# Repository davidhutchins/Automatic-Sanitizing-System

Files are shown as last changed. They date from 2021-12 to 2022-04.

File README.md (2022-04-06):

# Automatic-Sanitizing-System
## IoT Automatic Door-Handle Cleaning System

By David Hutchins, Austin Welch, Branden Evangelista, Alejandro Jacobo, and Brontë Cadogan

## Synopsis
The Automatic Handle Cleaning System (A.H.C.S. for short) is a senior design project that attempts to help make the world a more sanitary place. Inspired by the COVID-19 pandemic and its call for a higher degree of sanitation, the A.H.C.S. uses embedded electronics and UV-C lights to detect motion and disinfect door handles as people use them. The entire system is battery powered, allowing for its use to disinfect any door handle, anywhere. The A.H.C.S. is internet enabled, and each device sends its sensor data to the A.H.C.S. server, which allows user accounts to monitor each of their devices and track usage data. Users can use this data to better understand traffic throughout each of their buildings and learn how frequently each door is used over time. 

## Setup Guide
This guide is intended to help you set up your Automatic Handle Cleaning System (AHCS) device, connect it to the internet, and link it with your AHCS account. 

### Step 1: Power on AHCS in configuration mode
In this step, you will turn on the AHCS in configuration mode, where you can then edit its configuration settings. 
1.	Power off the AHCS if it is already on.
2.	Find the configuration button located on the top right of the AHCS and hold it down.
3.	While holding down the configuration button, power on the AHCS.
4.	If successful, the front-facing LED should now be lit yellow.
 
### Step 2: Enter the configuration webpage
This step will show you how to connect to your AHCS device and how to access its configuration page. 
1.	Once the LED is lit yellow, the AHCS will be hosting an Access Point (AP) through which you can connect to with any Wi-Fi enabled device with access to an internet browser (i.e. Chrome, Firefox, Safari).
2.	Connect to the AP named “AHCS-ID” where ID will be replaced with your device’s ID number. 
3.	Once connected, your device might say that your connection does not have internet access, this is okay. 
4.	In a browser, enter the URL handlesetup.net and proceed to the webpage. 
5.	Once the page loads, you can continue to the next step. 

### Step 3: Edit your AHCS’s configuration settings
In the configuration webpage, you can change the AHCS’s Wi-Fi configuration and take note of its ID and registration code. 
1.	Configure your AHCS’s Wi-Fi configuration under the Wi-Fi Configuration tab.
2.	Current SSID and Security correspond to the current network the AHCS is connected to and that network’s security settings.
3.	Enter the SSID, security type, and password of the network you want to connect to and click ‘Apply’. The Current SSID and Security variables at the top will then change.
4.	Head to the Registration tab and take note of the Registration Code and Device ID as these will be needed for the next step.
5.	Click ‘Exit and Restart Device’, the AHCS will then restart and attempt to connect to the Wi-Fi network it was configured to. This will take 15-30 seconds. 
6.	Upon successful connection, the AHCS’s front LED will turn blue. If it cannot connect to the network, it will turn green. If the light turns green start again from step 1 and try again, making sure all the configuration settings were set correctly. 
7.	If the LED is blue, continue to the next step. 

### Step 4: Link AHCS with account
Once the AHCS has connected to a network for the first time, you will be able to link the device to your account.
1.	Go to the AHCS website at http://3.91.185.66/ and sign in to your account. If you do not have one, make sure to create a new account before continuing. 
2.	Once signed in, navigate to the Add Device section on the homepage. 
3.	Enter the AHCS Device ID and Registration/Verification Code from earlier and select ‘Add Device’. 
4.	If successful, you will receive a prompt saying that the link was successful, if not, ensure you have connected your AHCS device to the internet at least once and you correctly entered the AHCS ID and Registration/Verification code. 
5.	Congratulations! You have successfully connected your AHCS device to the internet and linked it to your account! You can now view the AHCS device’s statistics and data on the ‘Sanitizing Statistics’ page. 

## For Development and Testing
### Embedded Code
#### Install CCS
1. Download CCS from https://www.ti.com/tool/download/CCSTUDIO
2. Proceed through the installer, when asked to select between full and custom installation, choose custom and click next
3. On 'Select Components' Select 'SimpleLink MSP432 low power + performance MCUs'
4. On the next page, select only 'Spectrum Digital Debug Probes and Boards'
5. Proceed until program is installed

#### In CCS
1. Go to File > Import 
2. Choose Code Composer Studio > CCS Projects
3. Clone/Download the repository and select Hardware > Hand-Sanitizing-System as the search directory
4. Select Hand-Sanitizing-System_MSP432 and Finish
5. Hit the hammer icon on the top left bar to build the project (if it is not compiling, ensure that (Active - Debug) appears next to the project name on the project explorer, you can do this by clicking on the project, which 'selects' it as the build target)

### Running the Automatic Hand Cleaning System App (Webapp) on a Local Machine
1. Make sure NodeJS is installed https://nodejs.org/en/
2. Download the repo from GitHub using 
    `git clone https://github.com/davidhutchins/Automatic-Sanitizing-System.git`
3. Install dependencies using: `npm i`
4. Open the command prompt and navigate to the folder containing the server.js file:
   `cd Automatic-Sanitizing-System/Server/sanitizingsystem/src/server`
5. Enter the command `node server.js` to connect to the MongoDB database
6. In another terminal, navigate to this folder:
   `cd Automatic-Sanitizing-System/Server/sanitizingsystem/src`
and run the application with `npm start`
7. In another terminal, navigate to this folder:
   `cd Automatic-Sanitizing-System/Server/sanitizingsystem/src`
and enter the command `node exserver.js` to connect to the Express backend

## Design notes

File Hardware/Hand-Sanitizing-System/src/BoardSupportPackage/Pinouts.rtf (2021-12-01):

HFXT
In: PJ.3
Out: PJ.2

LED I2C
SDA: P3.6
SCL: P3.7

SensorPack I2C
SDA: P6.4
SCL: P6.5

SensorPack OPT3001
IRQ Pin: P3.6

SensorPack TMP007
IRQ Pin: P5.2

SensorPack BMI160
IRQ Pin: P4.1 // Disabled for CC3100
MAG IRQ Pin: P4.6

SensorPack BME280
IRQ Pin: P5.0

LaunchPad
Reset Pin: RST
RED LED: P1.0
Red RGB LED: P2.0
Green RGB LED: P2.1
Blue RGB LED: P2.2
Left Button: P1.1
Right Button: P1.4

Joystick
X-axis: P6.0
Y-axis: P6.1
Press: P4.3

Buttons
Up: P4.4
Right: P4.5
Down: P5.4
Left: P5.5

CC3100
IRQ: P2.5
ANT1: P2.7
ANT2: P2.6
CS: P3.0
HIB: P4.1
CLK: P1.5
MOSI: P1.6
MISO: P1.7

LCD
TFT_CS P10.4
TP_CS P10.5
CLK P10.1
DIN P10.3
DOUT P10.2
TP_IRQ P4.0
Reset P10.0
Backlight VCC

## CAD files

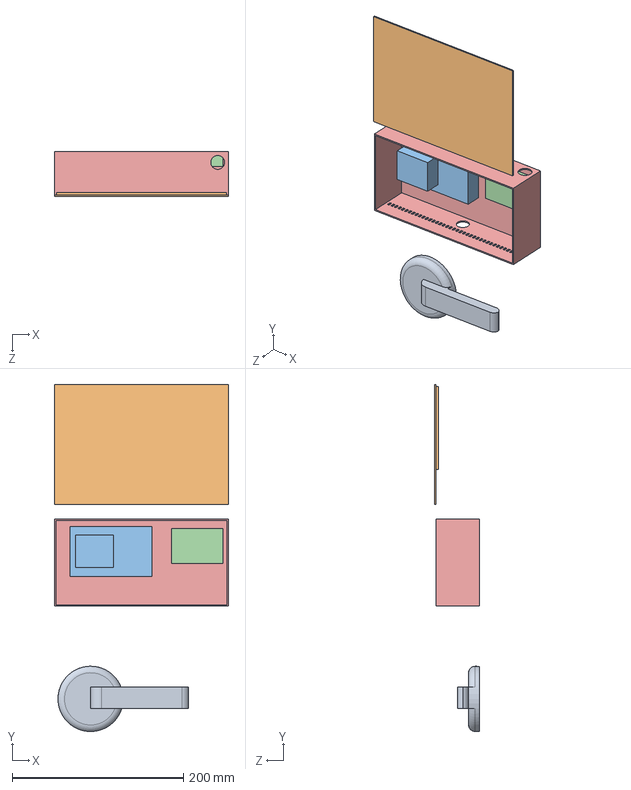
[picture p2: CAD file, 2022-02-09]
3-D Schematics/Assembly/Mockup_Assembly.SLDASM
203.2 x 404.7 x 52.4 mm
DoorHandle
Lid_V3
MCU
Prototype_Board
Housing_V3

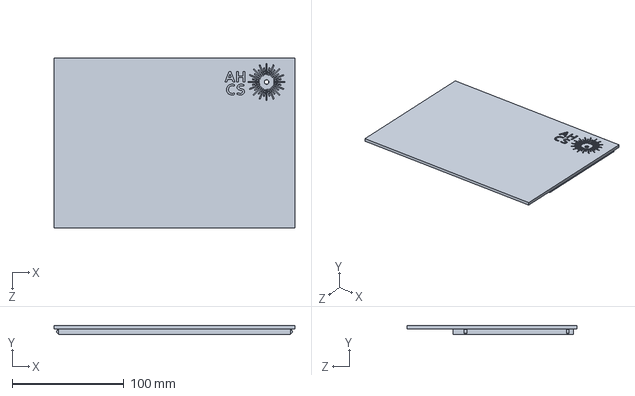
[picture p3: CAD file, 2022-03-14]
3-D Schematics/Parts/Lid_V4.SLDPRT
215.9 x 8.13 x 152.4 mm

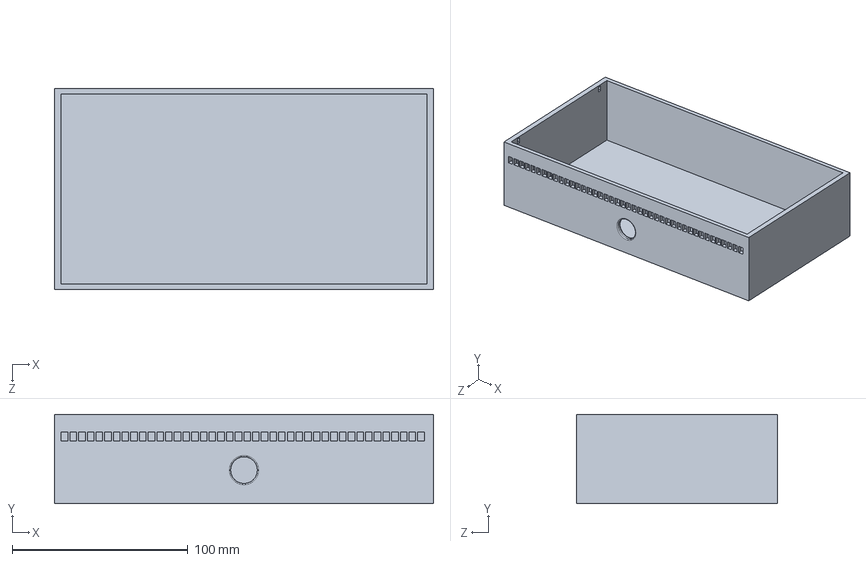
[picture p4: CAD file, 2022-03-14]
3-D Schematics/Parts/Housing_V4.SLDPRT
215.9 x 50.8 x 114.3 mm

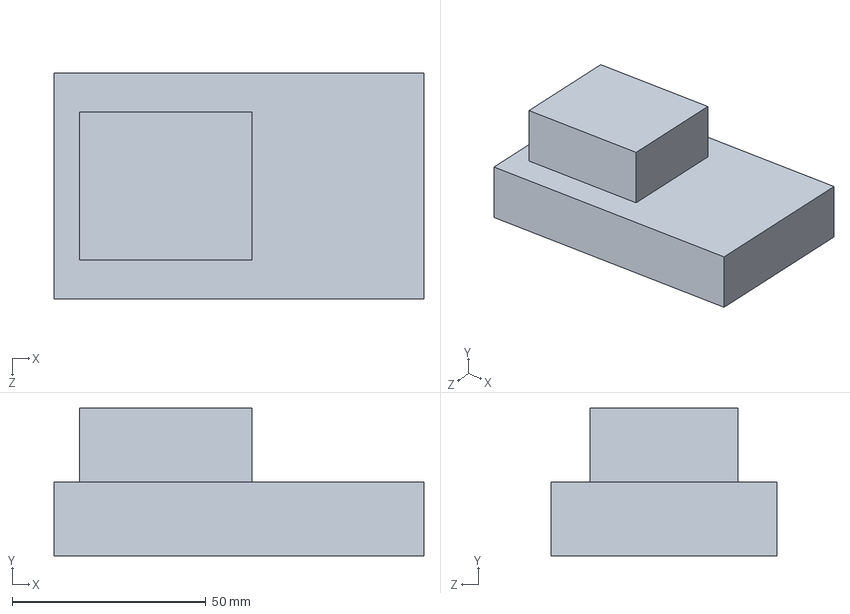
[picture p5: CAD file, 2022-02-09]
3-D Schematics/Parts/MCU.SLDPRT
95.5 x 38.1 x 58.4 mm

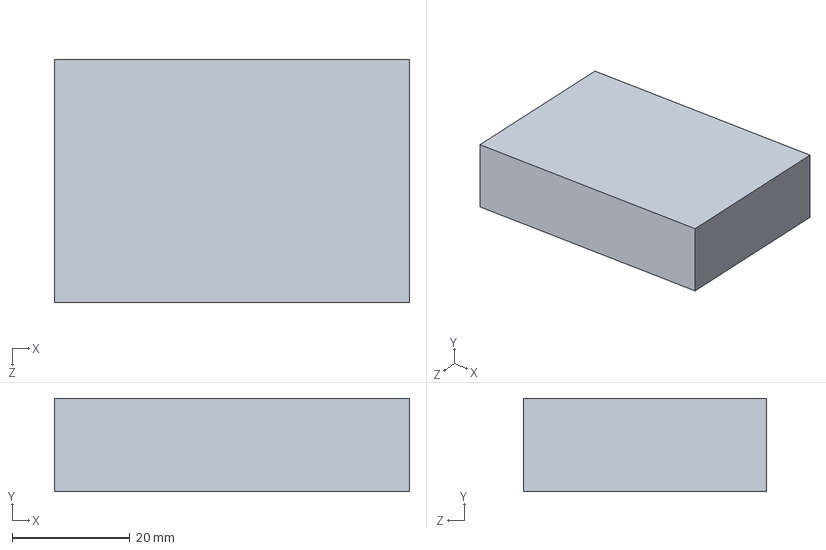
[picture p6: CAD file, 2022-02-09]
3-D Schematics/Parts/Prototype_Board.SLDPRT
60.3 x 15.9 x 41.3 mm

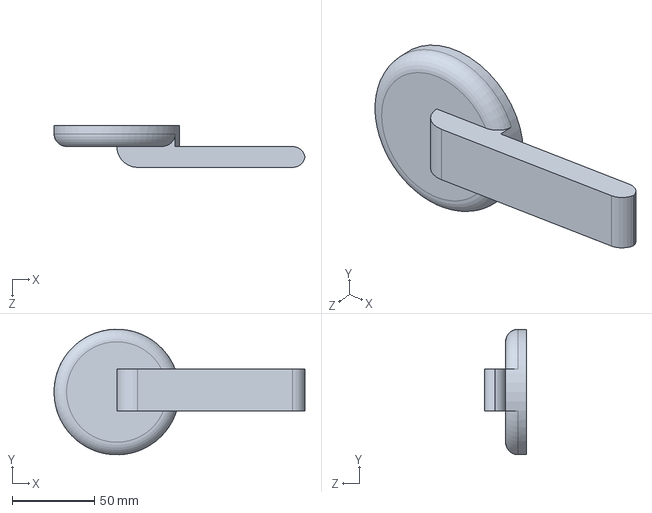
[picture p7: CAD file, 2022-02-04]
3-D Schematics/Parts/DoorHandle.SLDPRT
152.3 x 76.1 x 25.4 mm

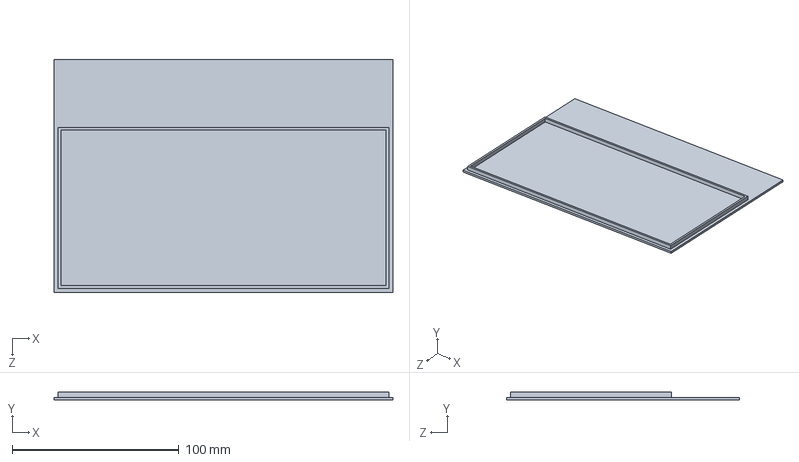
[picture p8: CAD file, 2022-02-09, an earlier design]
3-D Schematics/Parts/Lid_V3.SLDPRT
203.2 x 4.76 x 139.7 mm

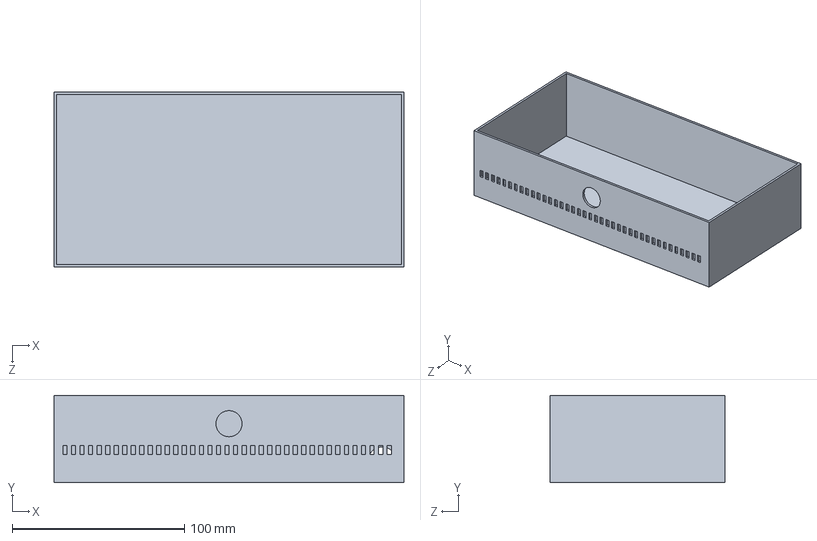
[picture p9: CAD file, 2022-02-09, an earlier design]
3-D Schematics/Parts/Housing_V3.SLDPRT
203.2 x 50.8 x 101.6 mm

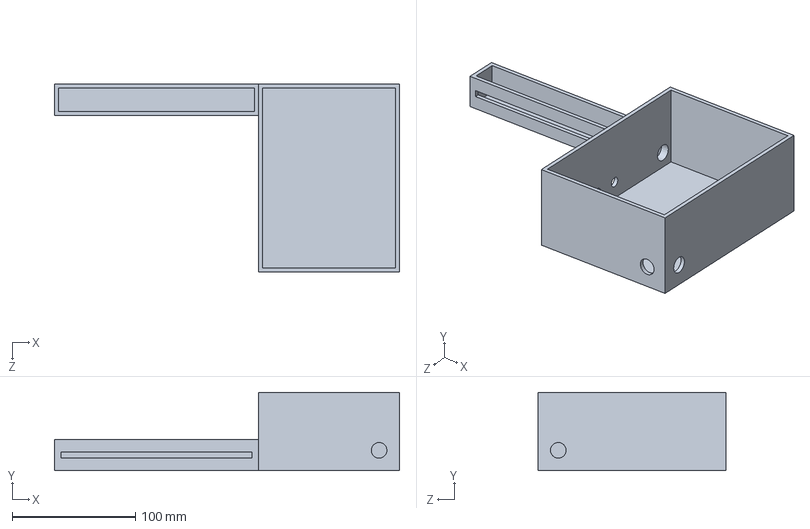
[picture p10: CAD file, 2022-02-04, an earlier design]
3-D Schematics/Parts/Housing_V1.SLDPRT
279.4 x 63.5 x 152.4 mm

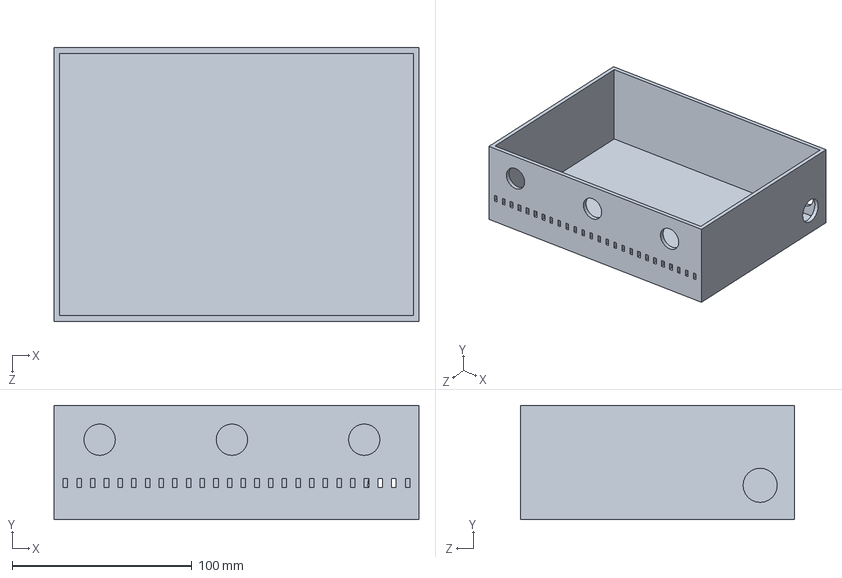
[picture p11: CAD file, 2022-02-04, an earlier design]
3-D Schematics/Parts/Housing_V2.SLDPRT
203.2 x 63.5 x 152.4 mm

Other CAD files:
3-D Schematics/Drawings/Housing_V4.SLDDRW
3-D Schematics/Drawings/Lid_V4.SLDDRW

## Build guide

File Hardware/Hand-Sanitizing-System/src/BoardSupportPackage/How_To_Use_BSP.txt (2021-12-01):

BSP Notes:

	Raz's Drivers

	BSP:
		Init Entire Board:
			BSP_InitBoard(): calls all subsequent initialization functions

	ClockSys:
		Init: ClockSys_SetMaxFreq() (Sets MCLK to 48MHz, HSMCLK to 24MHz, and SMCLK to 12 MHz)
		Read Data: ClockSys_GetSysFreq() (Gets MCLK Speed in MHz) 

		Problems/Concerns: None at the momemnt
		Future Improvements: Configurability? (Difficult when trying to sync using peripherals)

	BackChannelUART
		Init: BackChannelInit(): Set's up backchannel UART to communicate at 115200 Baud with 1 Start bit, 8 data bis, and 1 Stop bit
		
		Print Text: BackChannelPrint(string, textStyle)
			Prints a string in json format with specfic textStyle enumeration

		BackChannelPrintIntVariable:
			Prints an integer variable name and value in json format

		BackChannelEventTrigger:
			Prints an event trigger in JSON format

	TI's Drivers

	Opt3001: (Light Sensor) 
		Init: [initI2C must be called beforehand] sensorOpt3001Enable(true)
		Read Data: sensorOpt3001Read(uint16_t *rawData)

		Problems/Concerns: Does not use interrupt to signal processor that data is ready. Simply returns false if failed. Wasted CPU time
		Future Improvements: Enable Port to receive intrrupts from sensor. Big CPU saver

	Tmp007:
		Init: [initI2C must be called beforehand] sensorTmp007Enable(true)
		Read Data: sensorTmp007Read(uint16_t *rawTemp, uint16_t *rawObjTemp)

		Problems/Concerns: Does not use interrupt to signal processor that data is ready. Simply returns false if failed. Wasted CPU time
		Future Improvements: Enable Port to receive intrrupts from sensor. Big CPU saver

	Bosch's Drivers

	Bmi160:
		A LOT of things going on here. BoschSensorTec has some SUPER configurable code (resulting in tens of thousands of lines of code though -_-)

		There are 2 libraries: bmi160 and bmi160_support
			bmi160 is the full api containing every single possible function for messing with this thing. 
			bmi160_support contains example functions, public data structures, and compound api calls.

		Main Struct: bmi160_t - Holds valuable information such as chip id, device address, WriteFunctionPTR, ReadFunctionPTR, BurstWriteFunctionPtr, DelayMSFunction

		To Initialize the bmi160, you must first initialize the bmi160_t struct with all fields except chip id.
		Then Call bmi160_init which will test out the reading and writing as well as get the chip id and link the struct pointer into the library.

		*** ALL OF THIS CAN BE ACCOMPLISHED BY CALLING bmi160_initialize_sensor() ****

		After initializing, we need to configure the BMI160 to work the way we want. The Support Library provides a configuration function for setting the running mode bmi160_config_running_mode
		The following modes are possible:
				*      	    Description                |  value
 				*      --------------------------------|----------
 				*  	STANDARD_UI_9DOF_FIFO          |   0
 				*	STANDARD_UI_IMU_FIFO           |   1
				*	STANDARD_UI_IMU                |   2
 				*	STANDARD_UI_ADVANCEPOWERSAVE   |   3
 				*	ACCEL_PEDOMETER                |   4
 				*	APPLICATION_HEAD_TRACKING      |   5
 				*	APPLICATION_NAVIGATION         |   6
 				*	APPLICATION_REMOTE_CONTROL     |   7
 				*	APPLICATION_INDOOR_NAVIGATION  |   8

		*** NOTE Initialize Sensor sets it to 0 ***

		Reading Accelerometer Data:	You must first have a "struct bmi160_accel_t" type variable. 
		
		Call bmi160_read_accel_xyz(&accelData) where accelData is the address of your variable.
		*You can also get individual x,y,z values by calling bmi160_read_accel_[x,y,z] pass a 16 bit signed integer pointer

		Reading Gyro Data:		You must first have a "struct bmi160_gyro_t" type 

		Call bmi160_read_gyro_xyz(&gyroData) where gyroData is the address of your variable.
		*You can also get individual x,y,z values by calling bmi160_read_gyro_[x,y,z] pass a 16 bit signed integer pointer

		Reading Magnetometer Data:	You must first have a "struct bmi160_mag_t" type

		Call bmi160_read_mag_xyz(&magData, 0) where magData is the address of your variable and the 0 is a select for using the bmm150 magnetometer.
		* You can also get individual x,y,z values by calling bmi_read_mag_[x,y,z] pass a 16 bit signed integer pointer

		Problems/Concerns: A LOT of code! Interrupts also don't seem to be used
		Future Improvements: Cut code that is not needed. Enable interrupts to save CPU time

	Bme280:
		Also many things going on like the bmi160. Does NOT provide a support initialize code like the bmi160, but I made one in the support file

		There are 2 libraries: bme280 and bme280_support
			bmi280 is the full api containing every single possible function for messing with this thing. 
			bmi280_support contains example functions, public data structures, and compound api calls.

		Main Struct: bme280_t - Holds valuable information such as chip id, device address, WriteFunctionPTR, ReadFunctionPTR, BurstWriteFunctionPTR, DelayMSFunction, oversampling configurations

		To Initialize the bme280, you must first initialize the bme_t struct with all fields except hip id and link the struct pointer into the library.

		After primary initialization, we must set the power mode to normal (bme280_set_power_mode(BME280_NORMAL_MODE))
		Then we must set the oversampling rates for pressure, humidity, and temperature sensors		
				bme280_set_oversamp_pressure(BME280_OVERSAMP_2X)
				bme280_set_oversamp_humidity(BME280_OVERSAMP_1X)
				bme280_set_oversamp_temperature(BME280_OVERSAMP_4X)

		Finally, we set the standby time (the time that the sensor is in standby until it makes another reading) (bme280_set_standby_durn(BME280_STANDBY_TIME_1_MS))

		*** ALL OF THIS CAN BE ACCOMPLISHED BY CALLING bmi280_initialize_sensor() ****

		Reading Pressure:

		Call bme280_read_uncomp_pressure(&pressureVal) where pressureVal is an integer pointer to hold the resultant value. 
		You can convert the pressure to Pascals by calling bme280_compensate_pressure_int32()

		Reading Temperature:

		Call bme280_read_uncomp_temperature(&tempVal) where tempVal is an integer pointer to hold the resultant value. 
		You can convert the temperature to Celicius*100 by calling bme280_compensate_temperature_int32()

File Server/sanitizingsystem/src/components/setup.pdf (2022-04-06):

AH
CS | Setup Guide

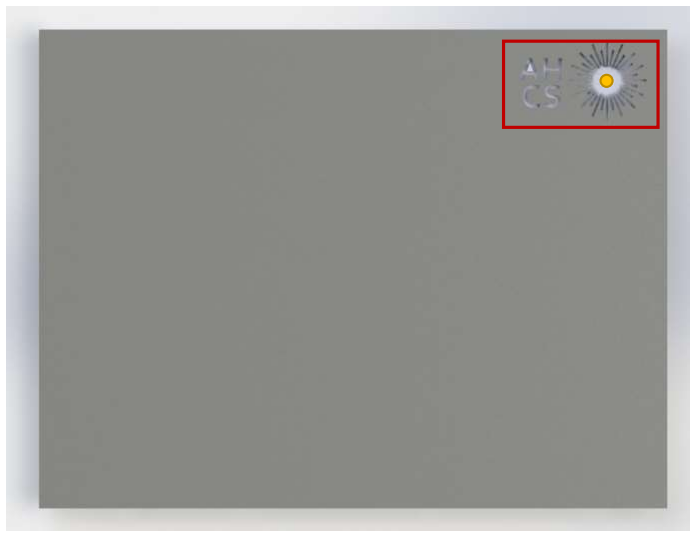
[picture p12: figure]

1

This guide is intended to help you set up your Automatic Handle Cleaning System (AHCS) device, connect it to the internet, and link it with your AHCS account.

## Step 1: Power on AHCS in configuration mode

In this step, you will turn on the AHCS in configuration mode, where you can then edit its configuration settings.
1. Power off the AHCS if it is already on.
2. Find the configuration button located on the top right of the AHCS and hold it down.
3. While holding down the configuration button, power on the AHCS.
4. If successful, the front-facing LED should now be lit yellow.

Figure 1. Front of the AHCS with the front LED lit yellow

## Step 2: Enter the configuration webpage

This step will show you how to connect to your AHCS device and how to access its configuration page.

AH
CS | Setup Guide

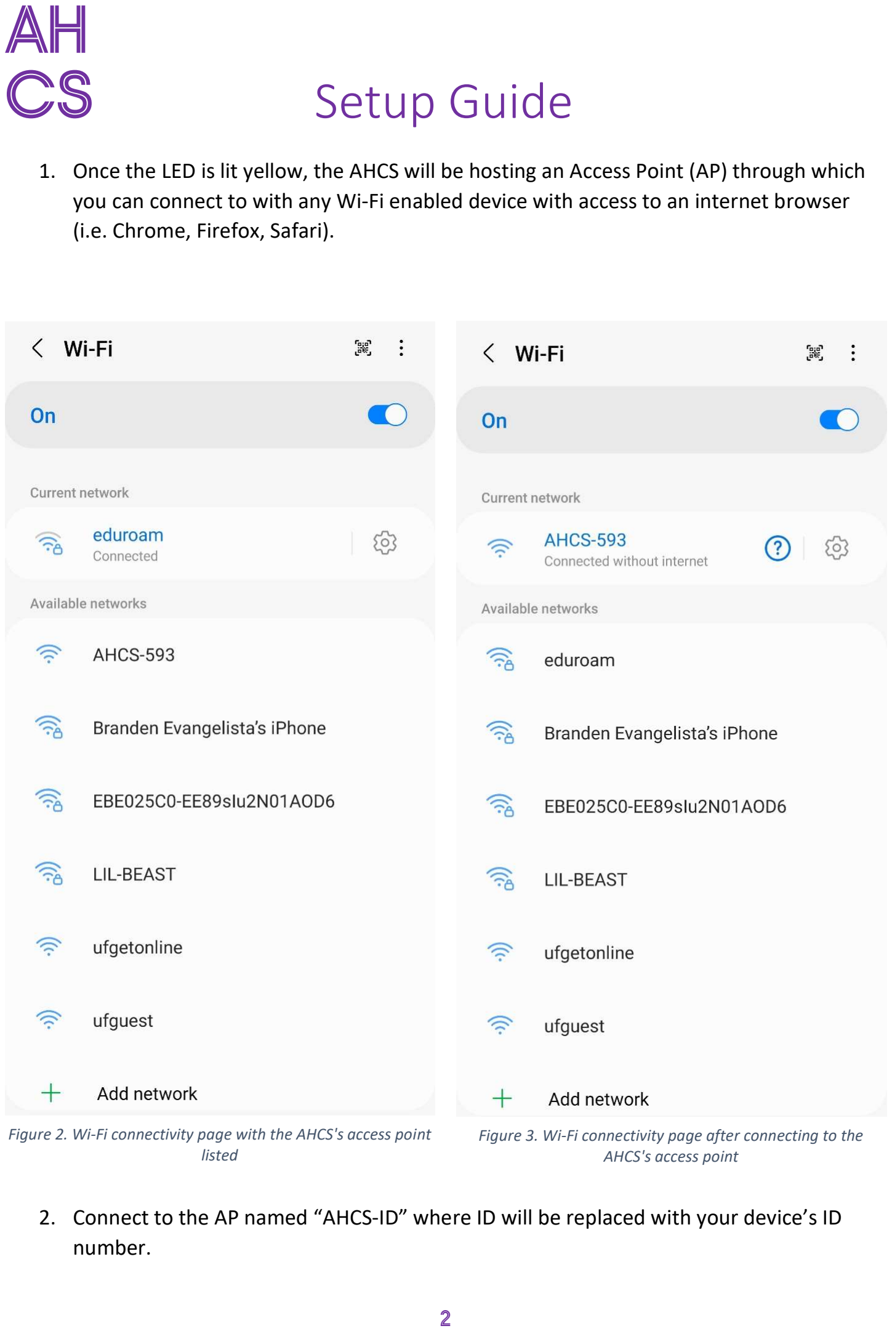
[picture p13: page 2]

2

1. Once the LED is lit yellow, the AHCS will be hosting an Access Point (AP) through which you can connect to with any Wi-Fi enabled device with access to an internet browser (i.e. Chrome, Firefox, Safari).

### 2. Connect to the AP named “AHCS-ID” where ID will be replaced with your device’s ID

number.

Figure 2. Wi-Fi connectivity page with the AHCS's access point
listed

Figure 3. Wi-Fi connectivity page after connecting to the AHCS's access point

AH
CS | Setup Guide

3

### 3. Once connected, your device might say that your connection does not have internet

access, this is okay.
4. In a browser, enter the URL handlesetup.net and proceed to the webpage.
5. Once the page loads, you can continue to the next step.

## Step 3: Edit your AHCS’s configuration settings

In the configuration webpage, you can change the AHCS’s Wi-Fi configuration and take note of its ID and registration code.

### 1. Configure your AHCS’s Wi-Fi configuration

under the Wi-Fi Configuration tab.

### 2. Current SSID and Security correspond to the

current network the AHCS is connected to and that network’s security settings.

### 3. Enter the SSID, security type, and password

of the network you want to connect to and click ‘Apply’. The Current SSID and Security variables at the top will then change.

### 4. Head to the Registration tab and take note

of the Registration Code and Device ID as these will be needed for the next step.

### 5. Click ‘Exit and Restart Device’, the AHCS will

then restart and attempt to connect to the Wi-Fi network it was configured to. This will take 15-30 seconds.

### 6. Upon successful connection, the AHCS’s

front LED will turn blue. If it cannot connect to the network, it will turn green. If the light turns green start again from step 1 and try again, making sure all the configuration settings were set correctly.
7. If the LED is blue, continue to the next step.

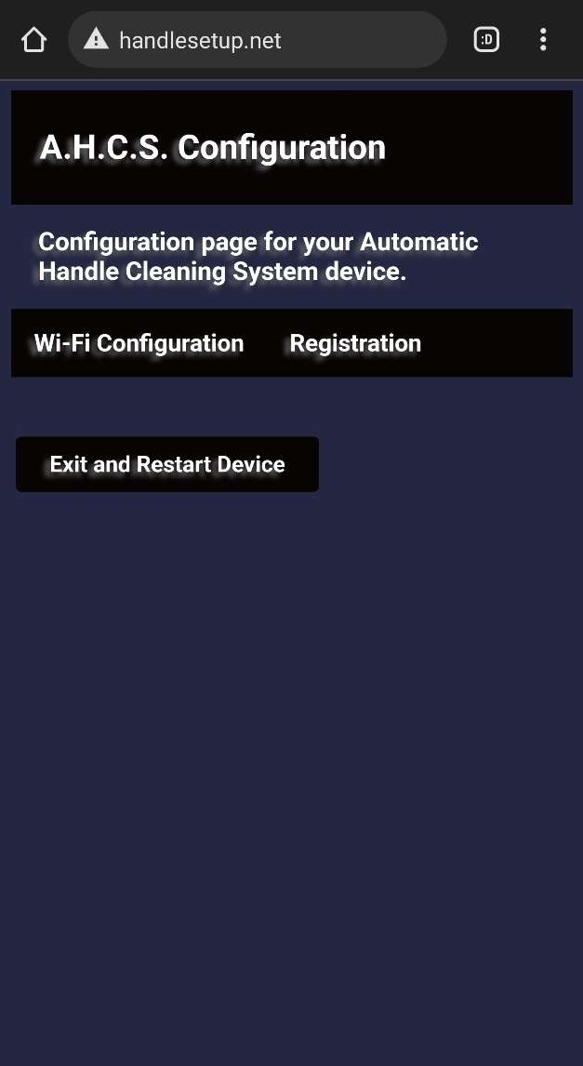
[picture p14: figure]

Figure 4. AHCS configuration webpage

AH
CS | Setup Guide

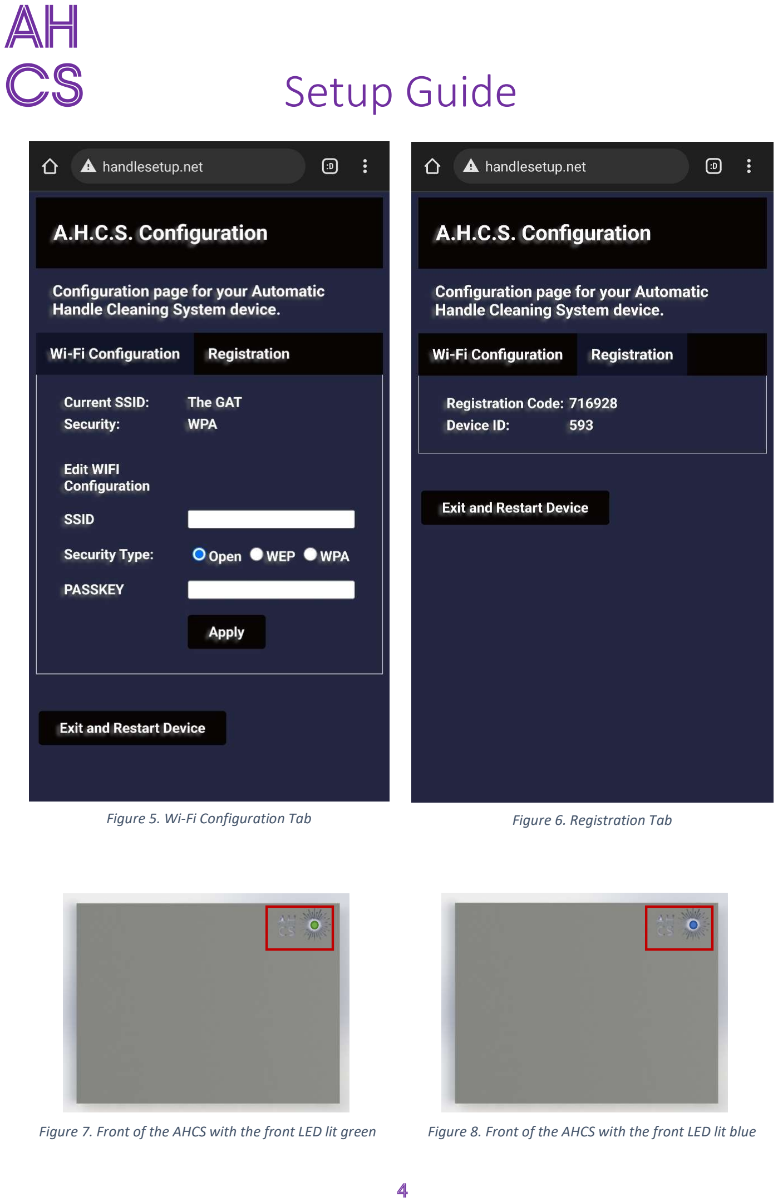
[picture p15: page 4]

4

Figure 7. Front of the AHCS with the front LED lit green | Figure 8. Front of the AHCS with the front LED lit blue
Figure 5. Wi-Fi Configuration Tab | Figure 6. Registration Tab

AH
CS | Setup Guide

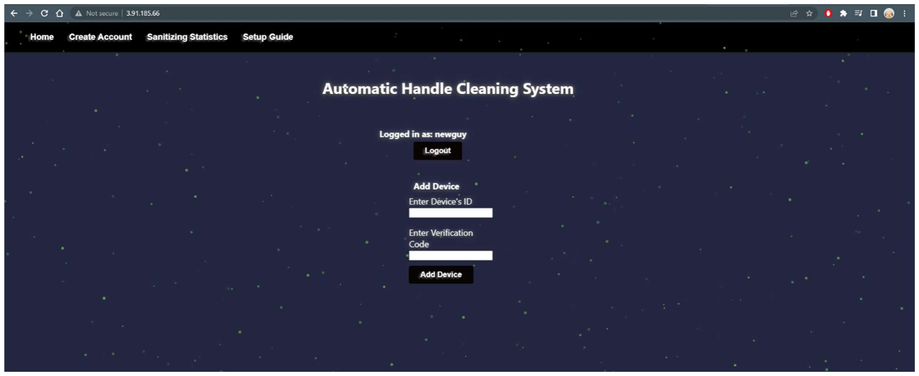
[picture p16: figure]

5

## Step 4: Link AHCS with account

Once the AHCS has connected to a network for the first time, you will be able to link the device to your account.
1. Go to the AHCS website at http://3.91.185.66/ and sign in to your account. If you do not have one, make sure to create a new account before continuing.
2. Once signed in, navigate to the Add Device section on the homepage.

### 3. Enter the AHCS Device ID and Registration/Verification Code from earlier and select

‘Add Device’.
4. If successful, you will receive a prompt saying that the link was successful, if not, ensure you have connected your AHCS device to the internet at least once and you correctly entered the AHCS ID and Registration/Verification code.

Figure 9. AHCS website's homepage once user is signed in.

AH
CS | Setup Guide

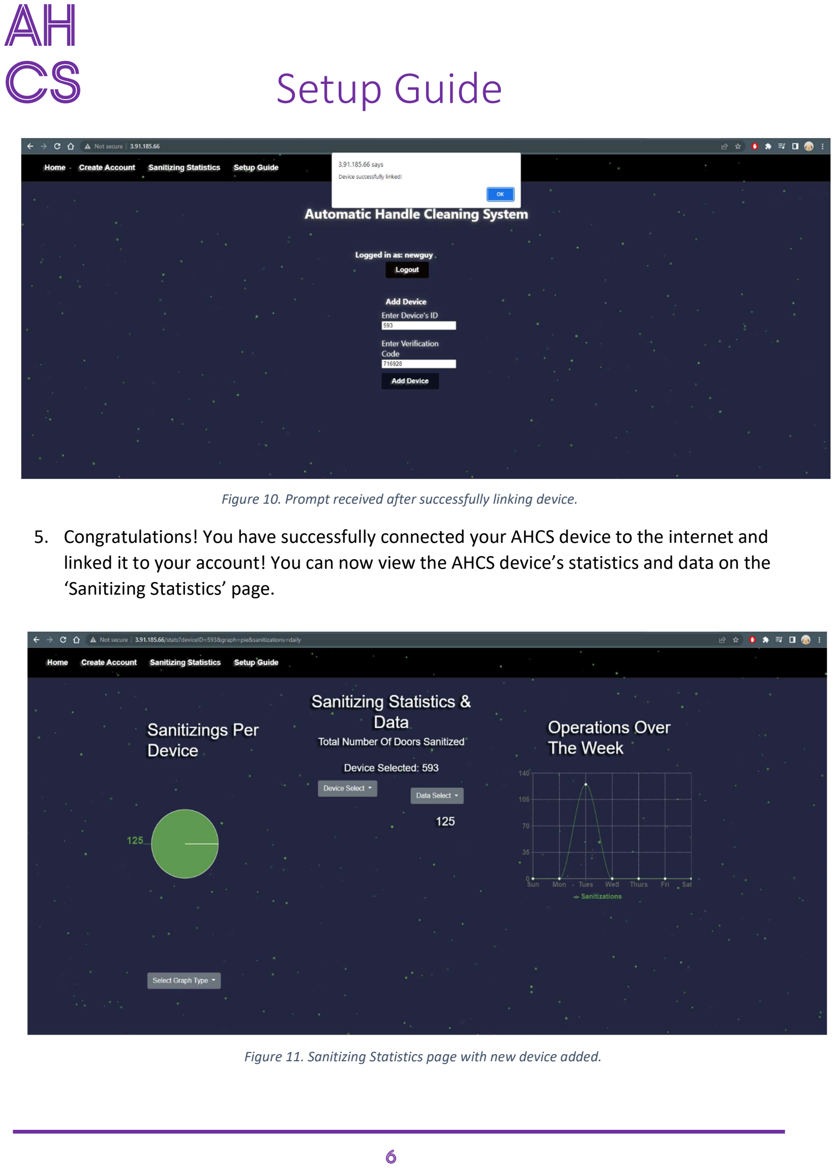
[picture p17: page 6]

6

### 5. Congratulations! You have successfully connected your AHCS device to the internet and

linked it to your account! You can now view the AHCS device’s statistics and data on the ‘Sanitizing Statistics’ page.

Figure 10. Prompt received after successfully linking device.

Figure 11. Sanitizing Statistics page with new device added.

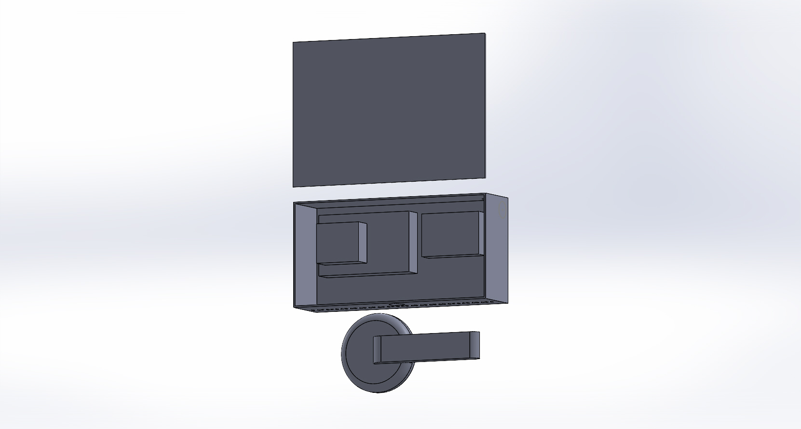
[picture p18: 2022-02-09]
3-D Schematics/Renders/Mockup_Assembly.JPG

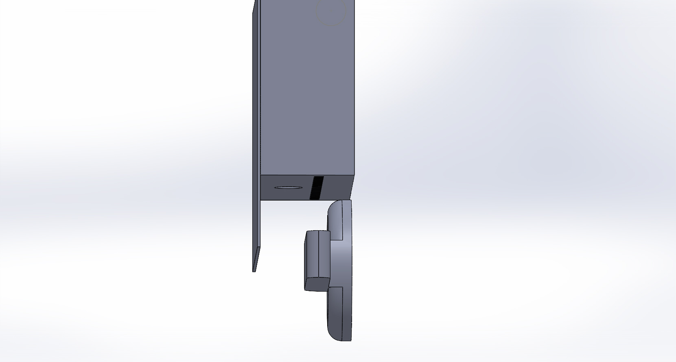
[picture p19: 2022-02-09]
3-D Schematics/Renders/Mockup_Assembly_3.JPG

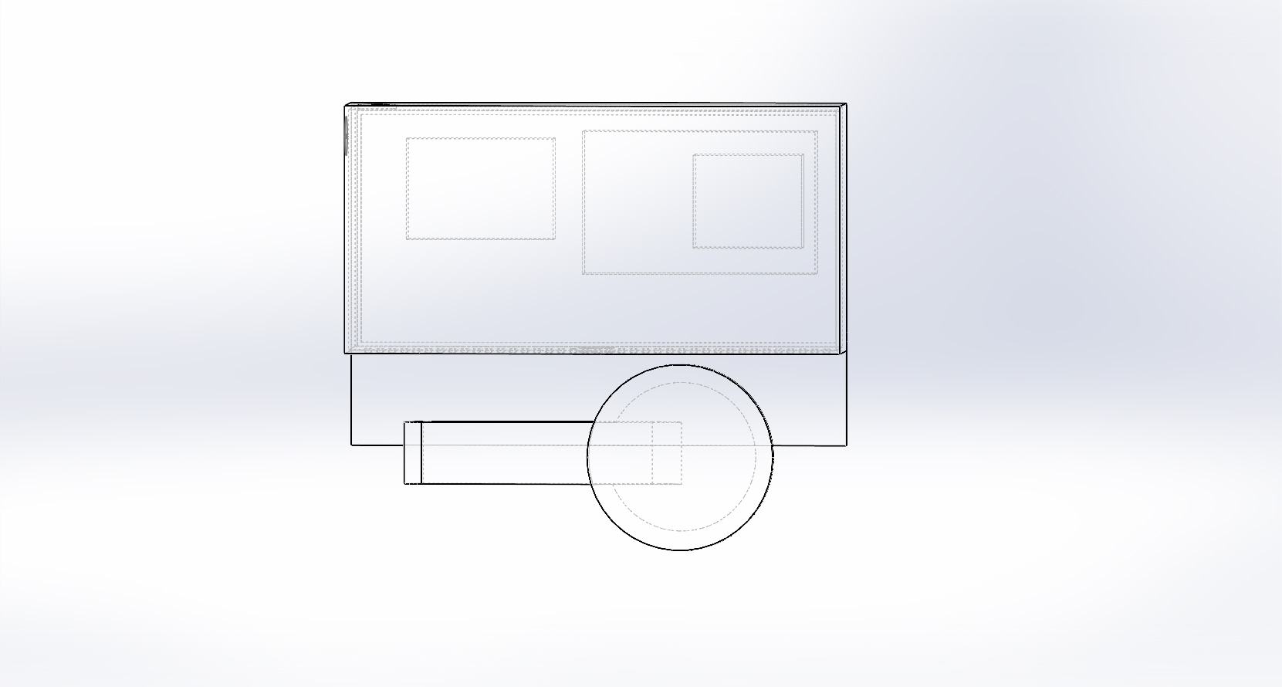
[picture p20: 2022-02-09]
3-D Schematics/Renders/Mockup_Assembly_2.JPG

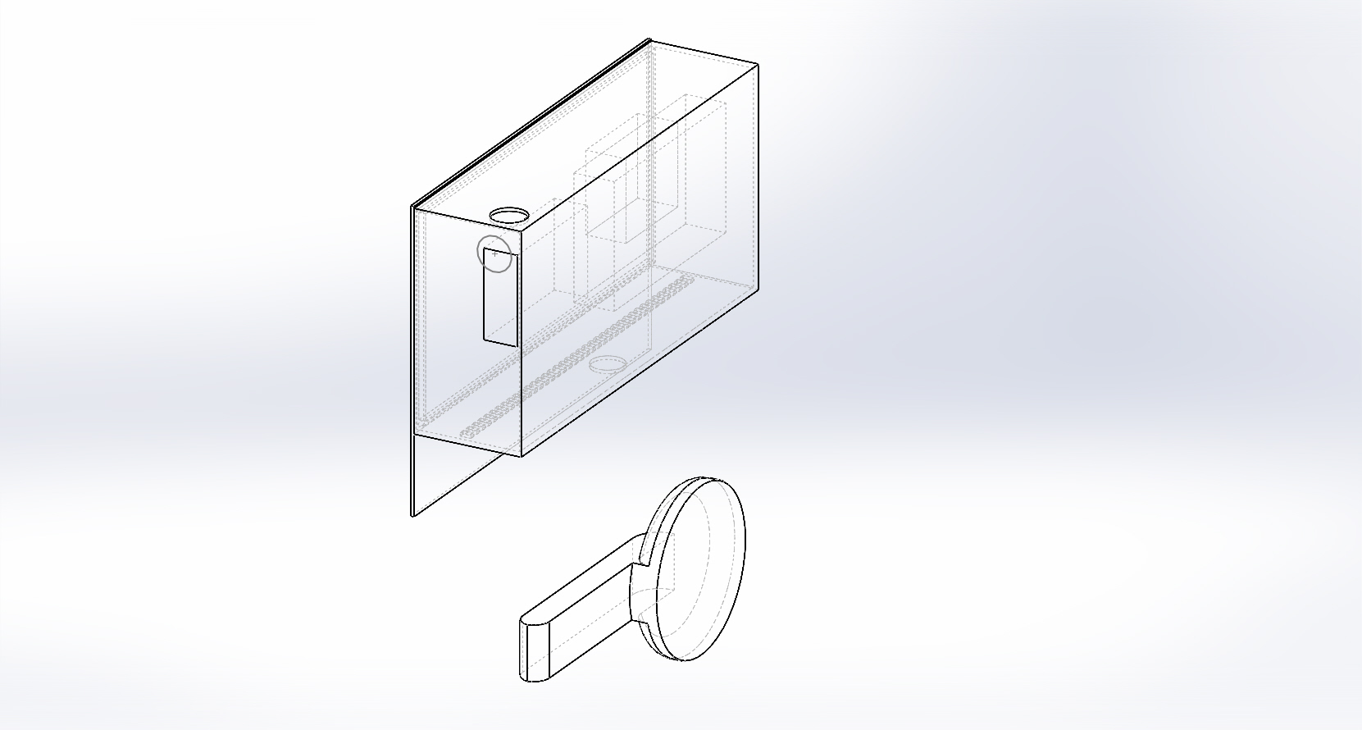
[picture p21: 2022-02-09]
3-D Schematics/Assembly/Mockup_Assembly_2.JPG

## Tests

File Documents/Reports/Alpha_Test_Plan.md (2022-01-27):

# Alpha Test Plan   

By David Hutchins, Austin Welch, Branden Evangelista, and Brontë Cadogan

## Specification

### Usability
#### Interface
For this alpha build, the web application pages have been updated, both in functionality and design. The statistics page has been revamped to display a line graph of the number of operations (i.e. the number of times the devices collectively trigger a UVC-light to turn on) over time. The statistics page also includes a pie chart to show the number of times each device (that is connected to the web application) is activated per week. The data to form these plots are pulled from a MongoDB database; the microcontroller(s) write to this database whenever the motion sensor triggers an interrupt to turn on the UVC-light. The setup guide page leads to a PDF that shows how to use our product; this PDF has been updated to show the instructions for building the web application on a local machine (instructions also included at the end of this report).

Interfacing with the UVC-light simply requires a hand motion in front of the motion sensor; the light will toggle on and off depending on whether a person's hand is in front of said sensor. The details outlining the sanitation process is in the "Responsiveness" section of this report.

For future iterations of the project, we should be able to connect more than one microcontroller to this web application and have these multiple devices write to the database concurrently.

#### Navigation
The web application is easy to navigate due to the navigation bar at the top of the web page. Users can switch between the home page, statistics page, setup guide page, and device connection page using this navigation bar.

For future builds, the UI will continue to be updated and will focus on the readability of data coming from the microcontroller. The web application will also aim to read connections from multiple devices.

#### Perception
The current iteration of the hardware (i.e. the microcontroller's connection to the WiFi backpack, bluetooth receiver, UVC-light, and motion sensor) are all connected on a breadboard. For future iterations, this breadboard will be consolidated into one PCB board; this board and our external power source will then be placed in a custom-made housing unit for a more simplistic look.

The product itself should be intuitive in design; users simply need to wave their hand in front of the motion sensor (which will be placed near a door handle) to activate the product's sanitation mode. Any interactions with the hardware will be documented on the web application's "Statistic" page. The data recorded by each microcontroller is consolidated in the statistic page's line graph and pie chart.

#### Responsiveness
The external interface makes use of hardware interrupts and software timers to control the use of the UVC-light. Whenever the motion sensor detects motion near the door handle, an interrupt will be triggered to tell the microcontroller to turn off the UVC-light. As long as the user's hand is over the sensor (or there is constant movement near the motion sensor), the UVC-light should turn off, representing the "safety mode" of the system. Once the user takes their hand away from the sensor, another interrupt will be triggered, turning the UVC-light back on. A software timer is then triggered, allowing the UVC to stay on for four seconds before turning back off again. This process is nearly the same as in the prototype; however, for this alpha build, we have incorporated the UVC-light and connected it to a MOSFET transistor. The MOSFET transistor acts like a switch, allowing us to control when the UVC-light will turn on and off (via the interrupts).

For future builds, this process will move from the breadboard to a PCB, which not only cleans up the aesthetic of the product.

### Build Quality
#### Robustness
In terms of robustness, the hardware is able to handle normal use case scenarios. The MOSFET we are using as a switch for the 24V UV-C LED strip is rated for 60V so usage for this product is well within its parameters. The current power source is connected to a wall socket so we are also well within the parameters for power draw. Migrating this to a portable power source will be a concern for robustness; however, the alpha build is robust in its power needs. Each component of the schematic has been tested individually and as a whole to make sure there are no points of failure on the hardware.

For the microcontroller, the interrupts and timers are robust and are resistant to unusual use cases on the MSP432. The timer can be interrupted before it runs through a full cycle and can smoothly transition to off for safety, and still operate correctly. The communication with our AWS server is as robust as the server itself and will work as long as both the network it is connected to and the server it runs on are up.

Our website will most likely be the least robust as it relies on external APIs and tools. Currently, the website has a basic and functional UI that does not allow too much user input so there are not many unusual use cases that can occur; thus, the website and its function are robust.

#### Consistency
Our system as a whole is consistent in its operation. When it detects movement, it activates an external signal that will enable the UV-C LEDs and send the usage to an AWS server. The website will consistently check for updated information from the database it uses.

#### Aesthetic Rigor
The hardware aesthetic as is will not cause any functional issues in its operation. The UI for the website is polished and provides a clean, consistent, and reliable experience. Unfinished aesthetics on the hardware will not inhibit functionality at all. The aesthetic of the website is established and will continue to be improved however in its current state, it is fully functional and gives a good impression of the final product. 

### Vertical Features
#### External Interface
Just like with the prototype, the external interface can be split into a hardware and software section.

The hardware section builds upon the circuit from the Design Prototype, except it makes use of the UV-C light. The interrupts will allow the state of the MOSFET transistor to be toggled which, when combined with the bidirectional level shifter, can provide 24V to the UV-C light with only a single 3.3V power source connected to the majority of the system.

The software section improves the UI and functionality of the web application. In particular, the web application can successfully read and display data from a MongoDB database. Eventually, the microcontroller will be able to send a ping to an AWS server, which will then be sent to the MongoDB database, allowing the website to track the number of times a microcontroller is used (i.e. an interrupt is sent to turn on the UV-C light).

#### Persistent State
The persistent state of the ACHS will be both the MongoDB database and the AWS web server. The web server will connect to the microcontroller’s WiFi backpack, allowing data from the microcontroller to be sent to this web server. This data will then be sent to the MongoDB database and subsequently be displayed on the web application. Data from the microcontroller will only be sent to the server and database if a user interacts with the motion sensor and turns on the UV-C light.

#### Internal Systems
The data processing comes from the microcontroller’s interaction with the AWS web server. The data that will be displayed on the web application will be the number of times the user interacts with the hardware; this count comes in the form of a ping from the microcontroller to the WiFi backpack. The number of pings the microcontroller sends out is subsequently stored in an AWS server.

For future builds, the AWS server should be able to handle pings from multiple microcontrollers simultaneously, which would allow multiple ACHS products to connect to the web application concurrently. Each product should send out a different ping, allowing the web application to track the use of each device individually.

## Links
- Repo: https://github.com/davidhutchins/Automatic-Sanitizing-System
- Google Drive: https://drive.google.com/drive/u/1/folders/1yFWsin02HhbcQPVtgGXrDhR7vxmtbRYc

## Build Instructions
### Install CCS
1. Download CCS from https://www.ti.com/tool/download/CCSTUDIO
2. Proceed through the installer, when asked to select between full and custom installation, choose custom and click next
3. On 'Select Components' Select 'SimpleLink MSP432 low power + performance MCUs'
4. On the next page, select only 'Spectrum Digital Debug Probes and Boards'
5. Proceed until program is installed

### In CCS
1. Go to File > Import 
2. Choose Code Composer Studio > CCS Projects
3. Clone/Download the repository and select Hardware > Hand-Sanitizing-System as the search directory
4. Select Hand-Sanitizing-System_MSP432 and Finish
5. Hit the hammer icon on the top left bar to build the project (if it is not compiling, ensure that (Active - Debug) appears next to the project name on the project explorer, you can do this by clicking on the project, which 'selects' it as the build target)

## Running the Automatic Hand Cleaning System App (Webapp) on a Local Machine
1. Make sure NodeJS is installed https://nodejs.org/en/
2. Download the repo from GitHub using 
    `git clone https://github.com/davidhutchins/Automatic-Sanitizing-System.git`
3. Install dependencies using: `npm i`
4. Open the command prompt and navigate to the folder containing the server.js file:
   `cd Automatic-Sanitizing-System/Server/sanitizingsystem/src/server`
5. Enter the command `node server.js` to connect to the MongoDB database
6. In another terminal, navigate to this folder:
   `cd Automatic-Sanitizing-System/Server/sanitizingsystem/src`
and run the application with `npm start`

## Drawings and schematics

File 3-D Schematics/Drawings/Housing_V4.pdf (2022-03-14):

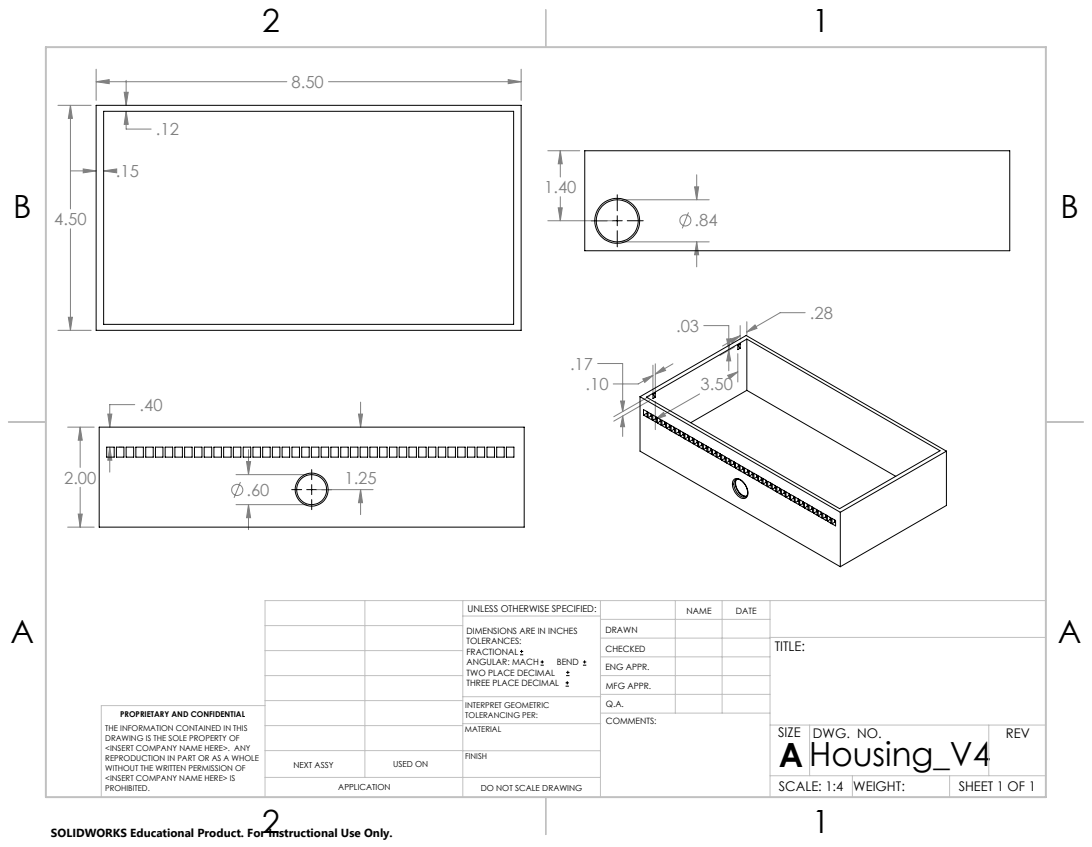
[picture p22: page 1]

UNLESS OTHERWISE SPECIFIED: | | NAME | DATE
DIMENSIONS ARE IN INCHES TOLERANCES: FRACTIONAL ANGULAR: MACH BEND TWO PLACE DECIMAL THREE PLACE DECIMAL | DRAWN

CHECKED | | | TITLE:

ENG APPR.
MFG APPR.

INTERPRET GEOMETRIC TOLERANCING PER: | Q.A.
MATERIAL | | SIZE A | DWG. NO. Housing_V4 | REV

PROPRIETARY AND CONFIDENTIAL
THE INFORMATION CONTAINED IN THIS
DRAWING IS THE SOLE PROPERTY OF
<INSERT COMPANY NAME HERE>. ANY
REPRODUCTION IN PART OR AS A WHOLE
WITHOUT THE WRITTEN PERMISSION OF
<INSERT COMPANY NAME HERE> IS
PROHIBITED.

NEXT ASSY | USED ON | FINISH

APPLICATION | DO NOT SCALE DRAWING | | SCALE: 1:4 | WEIGHT: | SHEET 1 OF 1

SOLIDWORKS Educational Product. For Instructional Use Only.

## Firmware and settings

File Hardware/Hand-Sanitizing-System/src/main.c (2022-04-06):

#include <msp432.h>
#include "wifi_functions.h"
#include "handleServer.h"
#include "led.h"
#include "BSP.h"

#define QUARTER_SECOND 46875
 
void gpio_init();
void timer_init();
void timer_start();
void timer_stop();
void safetyTimer_init();
void safetyTimer_start();
void safetyTimer_stop();
void UVC_on();
void UVC_off();

uint8_t count = 0;
uint8_t safetyCount = 0;
uint8_t activationFlag = 0;
uint8_t timerFlag = 0;
uint8_t safetyTimerFlag = 0;
uint8_t safetyTimerDone = 0;
uint8_t connectedToServer = 0;
uint8_t connectionConfigured = 0;
uint8_t breakSafetyLoop = 0;

int main(void)
{
	WDTCTL = WDTPW | WDTHOLD;
	
	BSP_InitBoard();
	timer_init();
	safetyTimer_init();
	gpio_init();

	LED_setColor(RED);
	PWM_set(6);
	PWM_init();
	PWM_start();
	NVIC_EnableIRQ(TA3_0_IRQn);

	if (P5->IN & BIT0) {
        LED_setColor(YELLOW);
        AP_init();
        connectionConfigured = 1;
        LED_setColor(RED);
    }

	connectedToServer = wifi_init();

	if (connectedToServer && connectionConfigured) {
	    sendRegistrationCode(DEVICE_ID, REG_CODE);
	}

	(connectedToServer) ?  LED_setColor(BLUE) :  LED_setColor(GREEN);

	NVIC_EnableIRQ(PORT3_IRQn);
	NVIC_EnableIRQ(TA0_0_IRQn);
	NVIC_EnableIRQ(TA1_0_IRQn);

	while(1) {
	    if (activationFlag) {
	        activationFlag = 0;
	        count = 0;

	        safetyCount = 0;
	        breakSafetyLoop = 0;
	        safetyTimer_start();
	        while(!safetyTimerDone && !breakSafetyLoop);
	        safetyTimerDone = 0;

	        if(breakSafetyLoop) {
	            breakSafetyLoop = 0;
	            continue;
	        }
        
          UVC_on();
          LED_setColor(PURPLE);

          if (connectedToServer) {
              uint8_t attempts = 0;
              while(incrementInteractionCounter(DEVICE_ID) == 0) { // Update handle interaction counter, quit after 3 tries, pass if not connected to WIFI
                  attempts++;
                  if (attempts == 3)
                      break;
              }
          }
          timer_start();
	    }
	 }
}


void gpio_init(void)
{
    // Ensure no pins are floating
    P1->OUT = 0x00; P1->DIR = 0xFF;
    P2->OUT = 0x00; P2->DIR = 0xFF;
    P3->OUT = 0x00; P3->DIR = 0xFF;
    P4->OUT = 0x00; P4->DIR = 0xFF;
    P5->OUT = 0x00; P5->DIR = 0xFF;
    P6->OUT = 0x00; P6->DIR = 0xFF;
    P7->OUT = 0x00; P7->DIR = 0xFF;
    P8->OUT = 0x00; P8->DIR = 0xFF;
    P9->OUT = 0x00; P9->DIR = 0xFF;
    P10->OUT = 0x00; P10->DIR = 0xFF;
    PJ->OUT = 0x00; PJ->DIR = 0xFF;


    P6DIR   = 0xFF;             // Set P6 as Output
    P6OUT   |= BIT0;            // Set BIT0 as high to start.

    P5DIR   &= ~BIT0;           // Set P5.0 as input
    P5OUT   &= ~BIT0;           // Set P5.0 as low to start.

    P3DIR   &= ~(BIT5 | BIT7);
    P3IFG   &= ~(BIT5 | BIT7);  // Setting up main mechanism and safety
    P3IES   |= BIT7;            // Bit 7 is high-to-low, main mechanism
    P3IES   &= ~BIT5;           // Bit 5 is low-to-high, safety mechanism
    P3IE    |= BIT5 | BIT7;     // Enabling both interrupts
    P3OUT   &= BIT5 | BIT7;

    P4DIR |= BIT0 | BIT2 | BIT4 | BIT5;
    P4OUT |= BIT0 | BIT2 | BIT4 | BIT5;
}

void timer_init(void)
{
    TA1CTL |= TASSEL_2 | ID_3;       // Configuring Timer A1 to SMCLK and Divider 8.
    TA1CCTL0 |= CCIE;                // Enabling interrupt for CC0 on Timer A1
    TA1EX0 |= (BIT2 | BIT1 | BIT0);  // Dividing by 8 a second time.
    TA1CCR0 = 0;                     // Timer will start when this is set to a nonzero value.
}

void timer_start(void)
{
    TA1EX0 |= (BIT2 | BIT1 | BIT0);  // Reset the clock divider
    TA1CTL |= MC_1;
    TA1CCR0 = QUARTER_SECOND;
}

void timer_stop(void)
{
    TA1CCR0 = 0;
    TA1CTL &= ~(BIT4 | BIT5);
}

void safetyTimer_init(void)
{
    TA0CTL |= TASSEL_2 | ID_3;        // Configuring Timer A1 to SMCLK and Divider 8.
    TA0CCTL0 |= CCIE;                 // Enabling interrupt for CC0 on Timer A1
    TA0EX0 |= (BIT2 | BIT1 | BIT0);   // Dividing by 8 a second time.
    TA0CCR0 = 0;                      // Timer will start when this is set to a nonzero value.
}

void safetyTimer_start(void)
{
    TA0EX0 |= (BIT2 | BIT1 | BIT0);   // Reset the clock divider
    TA0CTL |= MC_1;
    TA0CCR0 = QUARTER_SECOND;
}

void safetyTimer_stop(void)
{
    TA0CCR0 = 0;
    TA0CTL &= ~(BIT4 | BIT5);
}

void UVC_on(void)
{
    P6OUT &= ~BIT0;
}

void UVC_off(void)
{
    P6OUT |= BIT0;
}

// I/O Interrupt
void PORT3_IRQHandler()
{
    // Disable UV if light is currently on
    if (P3IFG & BIT5)       // Bit 5 is safety (low-to-high)
    {
       P3IFG &= ~BIT5;      // clearing the interrupt flag

       UVC_off();

       count = 0;
       safetyCount = 0;
       breakSafetyLoop = 1;

       safetyTimer_stop();
       timer_stop();
       (connectedToServer) ?  LED_setColor(BLUE) :  LED_setColor(GREEN);
    }

    // Enable UV
    else if (P3IFG & BIT7)  // Bit 7 is main mechanism (high-to-low)
    {
        P3IFG &= ~BIT7;     // clearing the interrupt flag
        activationFlag = 1;
    }
}

/****** Timer Interrupt ******/
void TA0_0_IRQHandler()
{
    TA0CCTL0 &= ~CCIFG;
    if (safetyCount < 12)  // With a clock time of .25 seconds. This will count for 3 seconds.
    {
        safetyCount++;
    }
    else
    {
        safetyCount = 0;
        safetyTimerDone = 1;
        safetyTimer_stop();
    }
}

void TA1_0_IRQHandler()
{
    TA1CCTL0 &= ~CCIFG;
    if (count < 120)       // With a clock time of .25 seconds. This will count for 30 seconds.
    {
        count++;
    }
    else
    {
        count = 0;
        UVC_off();         // Turn off light after time has passed
        timer_stop();      // Stop the timer
        (connectedToServer) ?  LED_setColor(BLUE) :  LED_setColor(GREEN);
    }
}

void TA3_0_IRQHandler()
{
    TA3CCTL0 &= ~CCIFG;
    PWMCount++;
    if (lightOn) {
       if (PWMCount >= PWMPercent) {
           lightOn = 0;
           P4OUT &= ~(BIT5);
           PWMCount = 0;
       }
    } else {
       if (PWMCount >= 100 - PWMPercent) {
           lightOn = 1;
           if (PWMPercent != 0)
               P4OUT |= BIT5;
           PWMCount = 0;
       }
    }

    // Cut down red brightness in mixed colors
    if (currentColor == PURPLE || currentColor == YELLOW) {
        if (redToggle) {
            redToggle = 0;
            P4OUT |= BIT0;
        } else {
            redToggle = 1;
            P4OUT &= ~(BIT0);
        }
    }
}

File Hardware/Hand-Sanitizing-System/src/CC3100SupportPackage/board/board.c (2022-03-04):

/*
 * board.c - msp430f5529 launchpad configuration
 *
 * Copyright (C) 2014 Texas Instruments Incorporated - http://www.ti.com/
 *
 *
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
 *    Redistributions of source code must retain the above copyright
 *    notice, this list of conditions and the following disclaimer.
 *
 *    Redistributions in binary form must reproduce the above copyright
 *    notice, this list of conditions and the following disclaimer in the
 *    documentation and/or other materials provided with the
 *    distribution.
 *
 *    Neither the name of Texas Instruments Incorporated nor the names of
 *    its contributors may be used to endorse or promote products derived
 *    from this software without specific prior written permission.
 *
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
*/

#include "simplelink.h"
#include "board.h"
#include "driverlib.h"

#define XT1_XT2_PORT_SEL0            PJSEL0
#define XT1_XT2_PORT_SEL1            PJSEL1
#define XT1_ENABLE                  (BIT0 + BIT1)
#define XT2_ENABLE                  (BIT2 + BIT3)
#define XT1HFOFFG   0

P_EVENT_HANDLER                pIraEventHandler = 0;

unsigned char IntIsMasked;


#ifdef SL_IF_TYPE_UART
#define ASSERT_UART(expr) {  if (!(expr)) { while(1) ;}}

unsigned char error_overrun = FALSE;
_uartFlowctrl uartFlowctrl;
_uartFlowctrl *puartFlowctrl = &uartFlowctrl;
#endif







int registerInterruptHandler(P_EVENT_HANDLER InterruptHdl , void* pValue)
{
    pIraEventHandler = InterruptHdl;

    return 0;
}


void CC3100_disable()
{
	P4OUT &= ~BIT1;
}


void CC3100_enable()
{
	// MSP432P401R = P4.1
	P4OUT |= BIT1;
}

void CC3100_InterruptEnable(void)
{
	// MSP432P401R = P2.5
    P2IES &= ~BIT5;
    P2IE |= BIT5;
    MAP_Interrupt_enableInterrupt(INT_PORT2);
    MAP_Interrupt_setPriority(INT_PORT2, 6);
    MAP_Interrupt_enableMaster();

}

void CC3100_InterruptDisable()
{
	// MMSP432P401R = P2.5
    P2IE &= ~BIT5;
    P2IFG &= ~BIT5;

    MAP_Interrupt_disableInterrupt(INT_PORT2);
#ifdef SL_IF_TYPE_UART
    UCA0IE &= ~UCRXIE;
#endif
}

void MaskIntHdlr()
{
    IntIsMasked = TRUE;
}

void UnMaskIntHdlr()
{
    IntIsMasked = FALSE;
}

void set_rts()
{
	// MSP432P401R = P5.6
	P5OUT |= BIT6;
}

void clear_rts()
{
	// MSP432P401R = P5.6
    P5OUT &= ~BIT6;
}

void initClk()
{
    /* Setup XT1 and XT2 */
    /* Configuring pins for peripheral/crystal usage and LED for output */
    MAP_GPIO_setAsPeripheralModuleFunctionOutputPin(GPIO_PORT_PJ,
            GPIO_PIN0 | GPIO_PIN1, GPIO_PRIMARY_MODULE_FUNCTION);

    /* Setting the external clock frequency. This API is optional, but will
     * come in handy if the user ever wants to use the getMCLK/getACLK/etc
     * functions
     */
    MAP_CS_setExternalClockSourceFrequency(32678,48000000);

    /* Starting LFXT in non-bypass mode without a timeout. */
    //CS_startLFXT(CS_LFXT_DRIVE3);

    /* Initializing MCLK to LFXT (effectively 32khz) */
    //MAP_CS_initClockSignal(CS_BCLK, CS_LFXTCLK_SELECT, CS_CLOCK_DIVIDER_1);
    //MAP_CS_initClockSignal(CS_ACLK, CS_LFXTCLK_SELECT, CS_CLOCK_DIVIDER_1);

    MAP_FlashCtl_setWaitState(FLASH_BANK0, 2);
    MAP_FlashCtl_setWaitState(FLASH_BANK1, 2);
    FLCTL->BANK0_RDCTL |= (FLCTL_BANK0_RDCTL_BUFI | FLCTL_BANK0_RDCTL_BUFD );
    FLCTL->BANK1_RDCTL |= (FLCTL_BANK1_RDCTL_BUFI | FLCTL_BANK1_RDCTL_BUFD );
    MAP_PCM_setPowerState(PCM_AM_DCDC_VCORE1);

    MAP_CS_setDCOCenteredFrequency(CS_DCO_FREQUENCY_48);
    MAP_CS_initClockSignal(CS_MCLK, CS_DCOCLK_SELECT, CS_CLOCK_DIVIDER_1 );
    MAP_CS_initClockSignal(CS_HSMCLK, CS_DCOCLK_SELECT, CS_CLOCK_DIVIDER_1 );
    MAP_CS_initClockSignal(CS_SMCLK, CS_DCOCLK_SELECT, CS_CLOCK_DIVIDER_1 );

    /* Globally enable interrupts */
    __enable_interrupt(); // @suppress("Function cannot be resolved")
}

void stopWDT()
{
    WDTCTL = WDTPW + WDTHOLD;
}

void initLEDs()
{
    P1OUT &= ~BIT0;
    P2OUT &= ~BIT2;
    P1DIR |= BIT0;
    P2DIR |= BIT2;
    P1SEL0 &= ~BIT0;
    P1SEL1 &= ~BIT0;
    P2SEL0 &= ~BIT2;
    P2SEL1 &= ~BIT2;
}

void turnLedOn(char ledNum)
{
    switch(ledNum)
    {
      case LED1:
        P1OUT |= BIT0;
        break;
      case LED2:
        P2OUT |= BIT2;
        break;
    }
}

void turnLedOff(char ledNum)
{
    switch(ledNum)
    {
      case LED1:
        P1OUT &= ~BIT0;
        break;
      case LED2:
        P2OUT &= ~BIT2;
        break;
    }
}


void toggleLed(char ledNum)
{
    switch(ledNum)
    {
      case LED1:
        P1OUT ^= BIT0;
        break;
      case LED2:
        P2OUT ^= BIT2;
        break;
    }

}

unsigned char GetLEDStatus()
{
  unsigned char status = 0;

  if(P1OUT & BIT0)
    status |= (1 << 0);
  if(P2OUT & BIT2)
    status |= (1 << 1);

  return status;
}

void initAntSelGPIO()
{
    P2OUT &= ~BIT7;
    P2OUT |=  BIT6; /* Select Antenna 1 */
    P2SEL0 &= ~(BIT6 + BIT7);
    P2SEL1 &= ~(BIT6 + BIT7);
    P2DIR |= (BIT6 + BIT7);
}

void SelAntenna(int antenna)
{
    switch(antenna)
   {
        case ANT1:
            P2OUT &= ~BIT7;
            P2OUT |=  BIT6;
            break;
        case ANT2:
            P2OUT &= ~BIT6;
            P2OUT |=  BIT7;
            break;
   }
}

//#pragma vector=PORT1_IRQHandler
//__interrupt
void PORT1_IRQHandler(void)
{
    /* Context save interrupt flag before calling interrupt vector. */
    /* Reading interrupt vector generator will automatically clear IFG flag */
	// P1 interrupt not required.

//    switch (__even_in_range(P1IV, P1IV_P1IFG7))
//    {
//        /* Vector  P1IV_NONE:  No Interrupt pending */
//        case  P1IV_NONE:
//            break;
//
//        /* Vector  P1IV_P1IFG0:  P1IV P1IFG.0 */
//        case  P1IV_P1IFG0:
//            break;
//
//        /* Vector  P1IV_P1IFG1:  P1IV P1IFG.1 */
//        case  P1IV_P1IFG1:
//            break;
//
//        /* Vector  P1IV_P1IFG2:  P1IV P1IFG.2 */
//        case  P1IV_P1IFG2:
//            break;
//
//        /* Vector  P1IV_P1IFG3:  P1IV P1IFG.3 */
//        case  P1IV_P1IFG3:
//            break;
//
//        /* Vector  P1IV_P1IFG4:  P1IV P1IFG.4 */
//        case  P1IV_P1IFG4:
//            break;
//
//        /* Vector  P1IV_P1IFG5:  P1IV P1IFG.5 */
//        case  P1IV_P1IFG5:
//            break;
//
//        /* Vector  P1IV_P1IFG1:  P1IV P1IFG.6 */
//        case  P1IV_P1IFG6:
//            break;
//
//        /* Vector  P1IV_P1IFG7:  P1IV P1IFG.7 */
//        case  P1IV_P1IFG7:
//            break;
//
//        /* Default case */
//        default:
//            break;
//    }
}

void Delay(unsigned long interval)
{
    while(interval > 0)
    {
        __delay_cycles(48000); // @suppress("Function cannot be resolved")
        interval--;
    }
}


/*!
    \brief          The IntSpiGPIOHandler interrupt handler

    \param[in]      none

    \return         none

    \note

    \warning
*/
//#pragma vector=PORT2_VECTOR
//__interrupt
void PORT2_IRQHandler(void)
{
    if (P2IFG & BIT5)
    {

#ifndef SL_IF_TYPE_UART
        if (pIraEventHandler)
        {
            pIraEventHandler(0);
        }
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

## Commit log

2021-11-18 Current changes 11/18/21
2021-11-22 Interrupt and Sensor/ LED interface working. TODO: Timer Implementation
2021-11-22 Interrupts working, INPROG: Timer Module
2021-11-29 Push current attempts to get WIFI working
2021-11-29 Developed Timer and interrupt enable
2021-12-01 Working prototype with MSP432
    TODO: Interface w/ server
2021-12-13 Fix server folder not merging properly
    [main.c]
2022-01-12 David and Branden: Research parts for PCB design. Imported/created components/chips necessary for schematic. Started making schematic (1/7/22-1/12/22)
    [CMT4502.SchLib, Senior_Design_PCB.PrjPcb, Sheet1.SchDoc]
2022-01-12 Working schematic for a mosfet with active low logic
2022-01-18 Grammar mistakes + formatting. Copied current work to a Google document
2022-01-22 Wifi module works with interrupt code
2022-01-25 Started adding logic for counting total pings across different connected devices
2022-01-28 Restructure Directory
    [CMT4502.SchLib, Senior_Design_PCB.PrjPcb, Sheet1.SchDoc]
2022-01-28 Moved to IRQ flagging model, moved sensor IRQ port
2022-01-30 Installed testing framework
2022-01-30 Modified package.json files for installed testing framework
2022-02-03 Fixed inconsistency in interrupts
    [main.c]
2022-02-04 Added v3 of housing
    [DoorHandle.SLDPRT, Housing_V1.SLDDRW, Housing_V1.SLDPRT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]
2022-02-08 Invert light activation signal
    [main.c]
2022-02-09 Updated Final 3d designs for printing
    [Housing_V3.SLDDRW, Housing_V3.SLDPRT, Housing_V3.STL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]
2022-02-11 Bronte/Branden Got the dropdown button working, we can now view daily weekly overall sanitizing datafor one device
2022-02-17 Move 3-D Schematics into Documents
    [DoorHandle.SLDPRT, Housing_V1.SLDDRW, Housing_V1.SLDPRT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]
2022-02-18 added login button to home page + styling
2022-02-18 login data flow should be good, doesnt work on my machine
2022-02-18 Random bug, suppressed to fix
    [board.c]
2022-02-28 Added hinges
    Added new hinge design that should work with our current form factor
    [DoorHandle.SLDPRT, Hinge_1.STL, Hinge_2.STL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]
2022-03-03 Make errors print to console
2022-03-03 Fixed bugs and cleaned up code, website functional
    - Got rid of connection issues switching from AP to station mode
    - Fixed issue where configuration settings were not being saved correctly
    - Added more test functionality
2022-03-14 Final print hopefully
    Thicker walls. snap fit, better design, logo
    [Hinge_1.STL, Hinge_2.STL, Housing_V1.SLDDRW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]
2022-03-16 Update main.c
    Changed the LED runtime from 4s -> 30s
2022-03-19 Case to deal with usernames with whitespace
2022-03-21 bronte/branden adding devices stage 1
2022-03-23 Fixed error page redirect edge case
2022-03-23 Add device registration feature
2022-03-24 Fix connection watchdog bug
    [main.c]
2022-03-24 Started creating new HTTP request for adding devices to specific accounts
2022-03-25 device ids can be added to database
2022-03-28 Finished refactoring backend to add users to device ID
2022-03-28 Fixed some edge cases + added another endpoint that filters via username
2022-03-28 Starting to make dynamic line chart by having user select a device id
2022-03-29 Added default device ID value when interacting with dropdown menus on stats page
2022-03-30 Added LED functionality
2022-04-04 Had to refactor backend to be compatible with Austin's code. Restyled buttons. Fix any logistics with UI
2022-04-05 Adjust LED brightness and pre-activation timer
2022-04-05 More bug fixes, refactoring
    [main.c]
2022-04-05 Fix final inconsistencies with device
    [main.c]
2022-04-06 Move restart button
